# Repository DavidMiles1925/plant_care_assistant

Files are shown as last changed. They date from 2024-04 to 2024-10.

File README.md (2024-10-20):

# Plant Care Assistant

## Video

[Project Video Link](https://www.youtube.com/watch?v=mg84hZeF66U&t=700s)
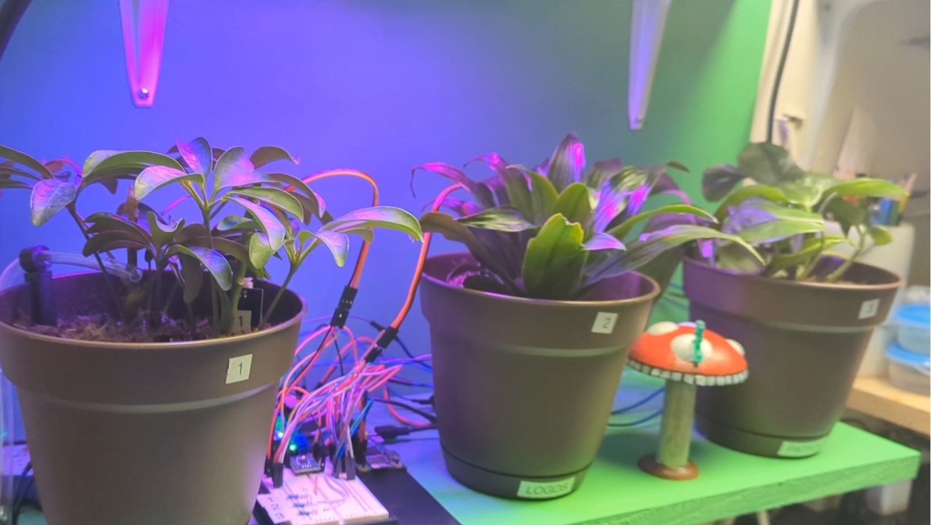
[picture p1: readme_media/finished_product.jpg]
Video Image


## Project Description

This project was developed to liven up my workspace. I wanted to have some plants, but historically I haven't kept them alive very well. I either over-water or under-water them. On top of that, my workspace gets no natural sunlight, so I wanted to make sure my plants got plenty of light. And lastly, my garage gets chilly in the winter, so I wanted my plants stay warm.

## Accepatance Criteria

**This project, when it is complete will:**

- ✔ Support up to 3 plants
- ✔ Monitor the moisture levels of the soil of each plant
- ✔ Water each plant when the soil is dry AND the soil has had an adequete period of dryness
- ✔ Provide adequete lighting for the plants with a timer function
- ✔ Log all metrics for debugging and historical reference
- **✔ NEW:** The amount of water dispensed can be counted from the logs programmatically

**Future State:**

- Provide gentle heat when soil temperature falls too low (future state)
- Smart lighting through feedback from a photo-resistor

## Seting up the Device

### Parts List

| Item | Quantity | Link |
| :--- | :---: | :--- |
| Raspberry Pi Zero 2 W (Any Pi will work) | 1 | [Microcenter](https://www.microcenter.com/product/643085/raspberry-pi-zero-2-w) |
| MicroSD card (For Raspberry Pi) | 1 | [Microcenter](https://www.microcenter.com/product/658767/micro-center-64gb-ultra-microsdxc-class-10-flash-memory-card-with-adapter) |
| 20x2 Pin Header for Raspberry Pi | 1 | [Microcenter](https://www.amazon.com/gp/product/B083DYVWDN/ref=ppx_yo_dt_b_search_asin_title?ie=UTF8&psc=1) |
| ADS7830 Analog-to-Digital Converter | 1 | No Link Available |
| Capacitive Moisture Sensor(s) |  1-3\* | [Amazon](https://www.amazon.com/gp/product/B07SYBSHGX/ref=ppx_yo_dt_b_search_asin_title?ie=UTF8&psc=1) |
| Water Pump(s) and Line |  1-3\* | [Amazon](https://www.amazon.com/gp/product/B07TMW5CDM/ref=ppx_yo_dt_b_search_asin_title?ie=UTF8&psc=1) |
| 5V USB Grow Light | 1 | [Amazon](https://www.amazon.com/gp/product/B0BXKWMTPF/ref=ppx_yo_dt_b_search_asin_title?ie=UTF8&psc=1) |
| 5V Relay |  2-4\* | [Amazon](https://www.amazon.com/gp/product/B09SLS3QT1/ref=ppx_yo_dt_b_search_asin_title?ie=UTF8&psc=1) |
| LED |  1-3\* | [Amazon](https://www.amazon.com/gp/product/B07QXR5MZB/ref=ppx_yo_dt_b_search_asin_title?ie=UTF8&psc=1) |
| 220 Ohm Reistor |  1-3\* | [Amazon](https://www.amazon.com/gp/product/B07ZX2CB6B/ref=ppx_yo_dt_b_search_asin_title?ie=UTF8&psc=1) |
| Solderless Breadboard | 1 | [Amazon](https://www.amazon.com/gp/product/B07PBFPJC6/ref=ppx_yo_dt_b_search_asin_title?ie=UTF8&psc=1) |
| Dupont Cables 10cm and 30cm | Many | [Amazon](https://www.amazon.com/gp/product/B01EV70C78/ref=ppx_yo_dt_b_search_asin_title?ie=UTF8&psc=1) |

\*Quantity is dependent on how many plants you want to care for.

### Diagram

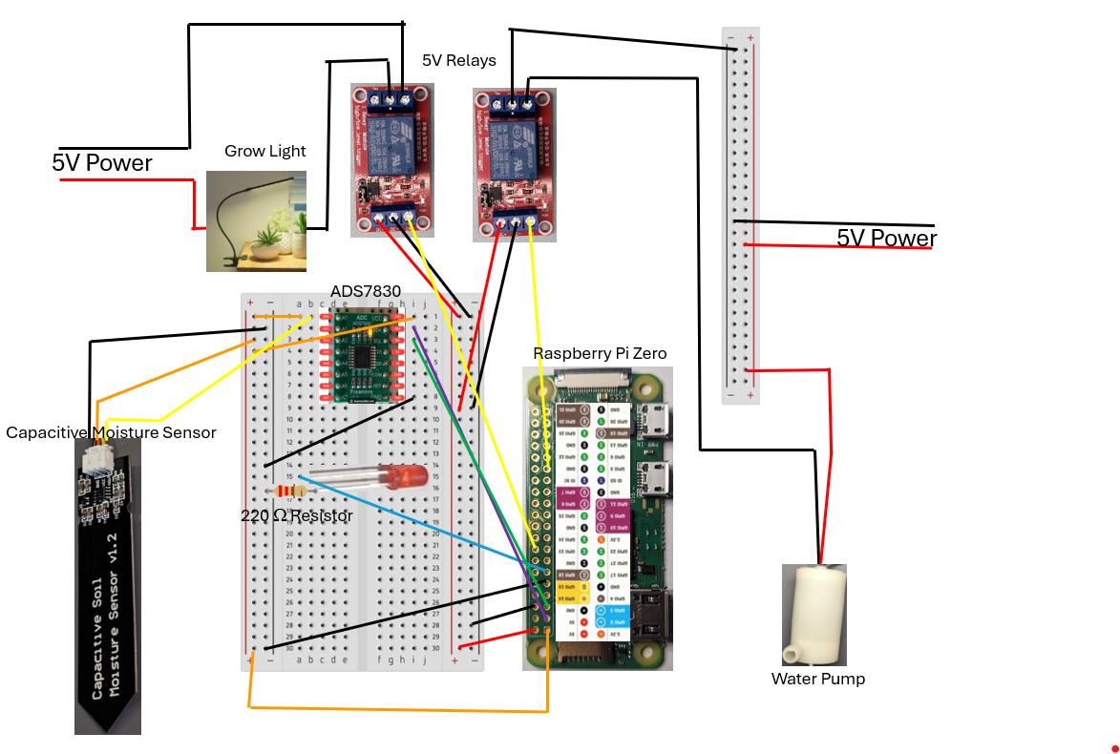
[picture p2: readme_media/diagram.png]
diagram


### Pin Assignments

**Note that all pins are in BCM mode**

| Component | Pi/Connection | Power |
| :--- | :---: | :---: |
| ADS7830 (or 1115) | 2, 3 |  3.3V (Pi) |
| Capacitive Moisture Sensor v 1.2 #1 | A0 (ADS) |  3.3V (Pi) |
| Capacitive Moisture Sensor v 1.2 #1 | A1 (ADS) |  3.3V (Pi) |
| Capacitive Moisture Sensor v 1.2 #1 | A2 (ADS) |  3.3V (Pi) |
| LED #1 | 17 |  3.3V (Pi) |
| LED #2 | 27 |  3.3V (Pi) |
| LED #3 | 22 |  3.3V (Pi) |
| Pump **Relay** #1 | 5 | 5V (Pi) |
| Pump **Relay** #2 (Optional) | 6 | 5V (Pi) |
| Pump **Relay** #3 (Optional) | 13 | 5V (Pi) |
| Light Relay #4 | 23 | 5V (Pi) |
| Water Pump #1 | Relay 1 | 5V (**USB**) |
| Water Pump #2 (Optional) | Relay 2 | 5V (**USB**) |
| Water Pump #3 (Optional) | Relay 3 | 5V (**USB**) |
| Light | Relay 4 | 5V (**USB**) |

### Set Up the Pi

[See my github tutorial on how to set up the Raspberry Pi Zero 2 W](https://github.com/DavidMiles1925/pi_zero_setup)

- If you want to run the code via SSH, make sure to also follow the instructions on that page on how to:
  [Set up a static IP address](https://github.com/DavidMiles1925/pi_zero_setup?tab=readme-ov-file#configure-static-ip-address)

### Set Up the Capacitive Moisture Sensor v1.2

1. Get the pins connected:  
   &emsp;See the [diagram](#diagram), [pin assignments](#pin-assignments), and [parts list](#parts-list) above.

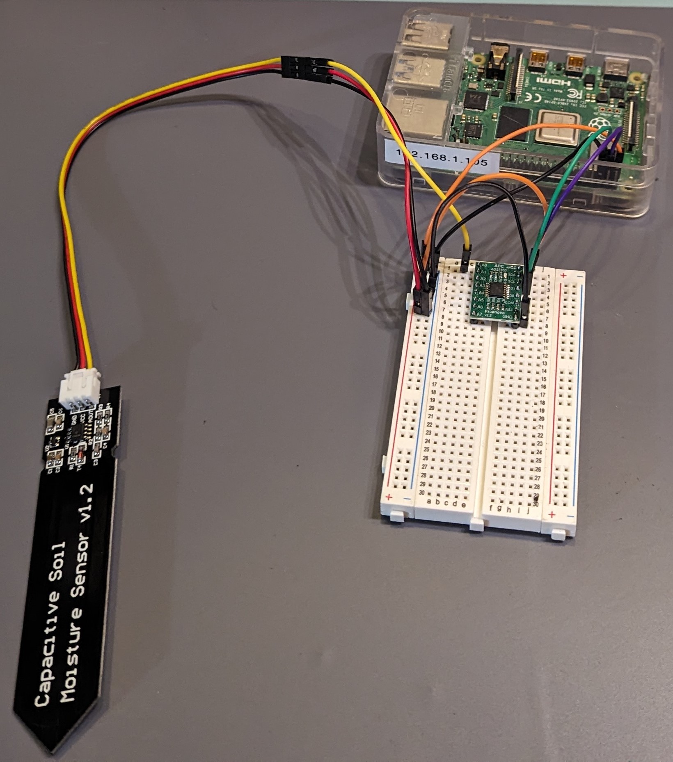
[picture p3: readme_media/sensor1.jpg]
sensor1

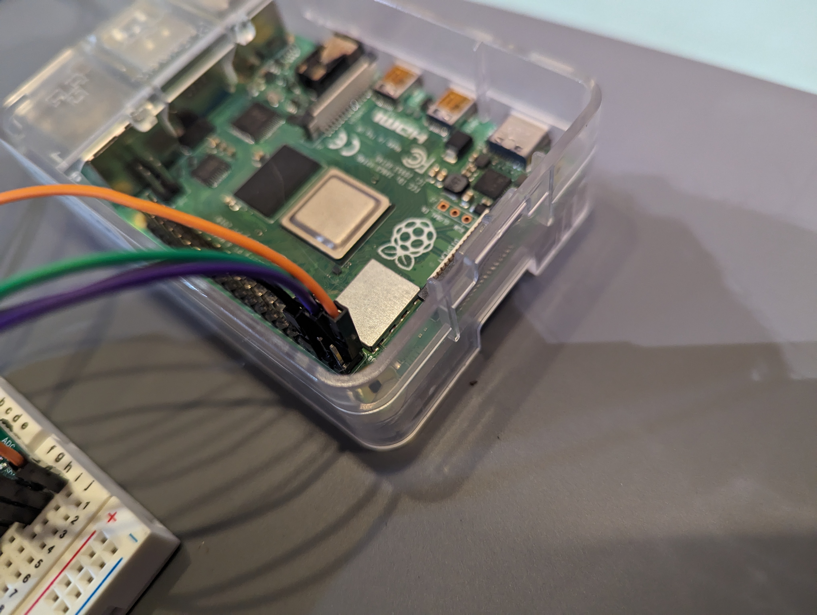
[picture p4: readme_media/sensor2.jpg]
sensor2


2. Make sure to calibrate your values with dry air, water, and everything in between (later after you get the code running):

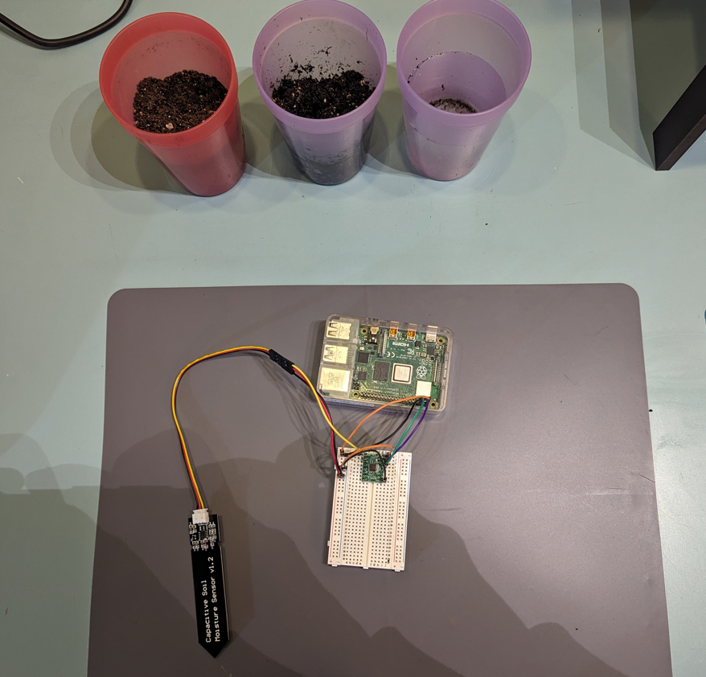
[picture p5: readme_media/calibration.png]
calibration


### Set Up Relays For Pumps

You'll need to wire up the relays as shown in the [diagram](#diagram).

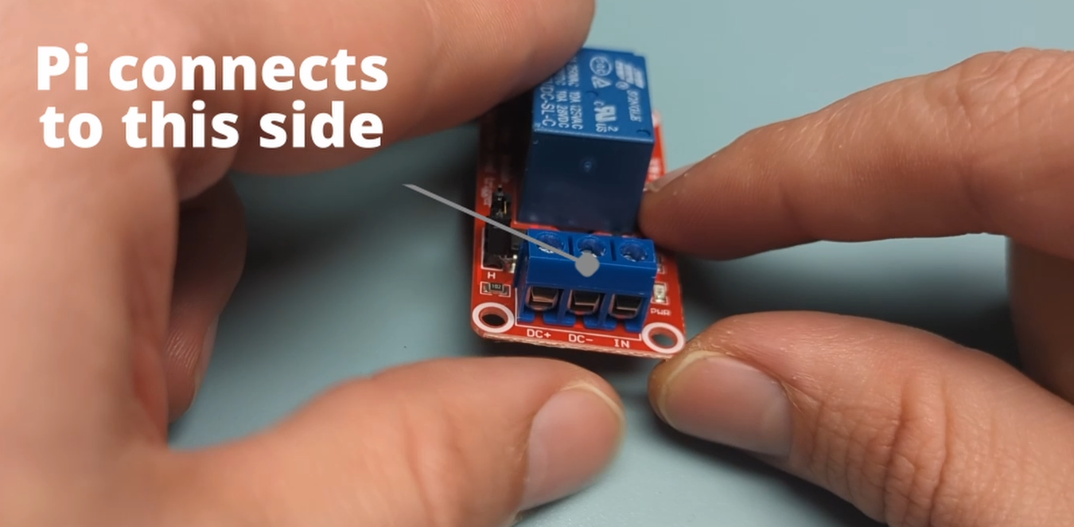
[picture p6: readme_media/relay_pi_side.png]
relay_pi_side


- `DC+` may be labeled as `VCC`
- `DC-` may be labeled as `GND`
- `IN` may be labeled as `PIN`

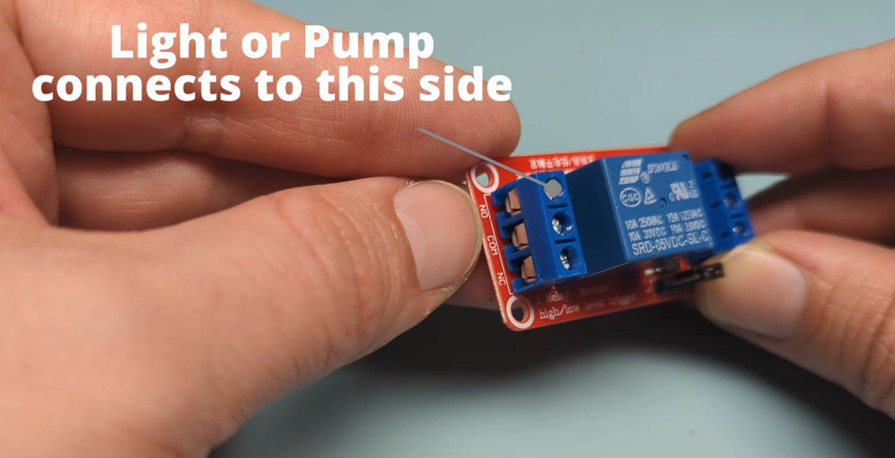
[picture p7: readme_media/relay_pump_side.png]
relay_pump_side


- Use the `NO` and `COM` ports. The NC port will turn the circuit on by default.

### Set Up the Pumps

1. Wire up the power for the pump using batteries or a USB cable. **DO NOT POWER THESE PUMPS DIRECTLY WITH THE PI!!!**

**See the [Video](#video) for tips on working with the tiny leads on the pump.**

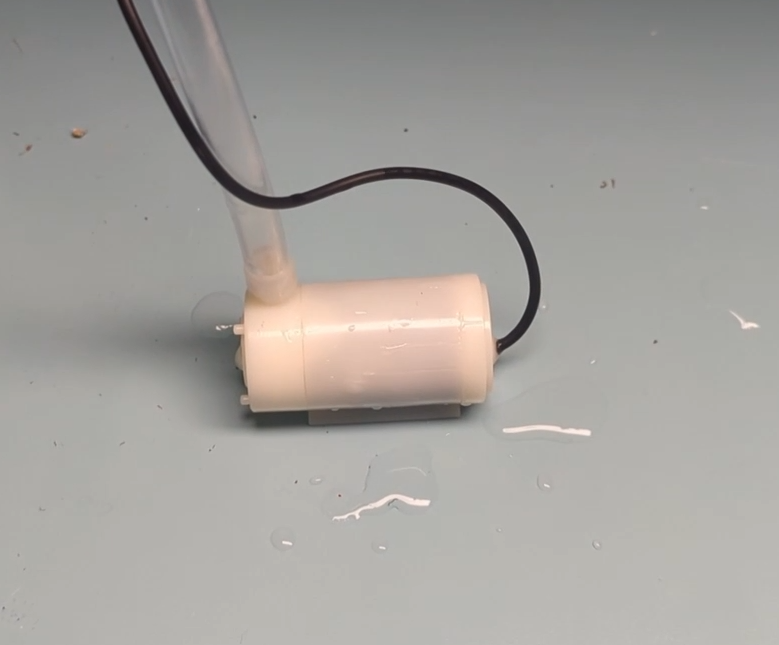
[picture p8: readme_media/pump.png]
pump

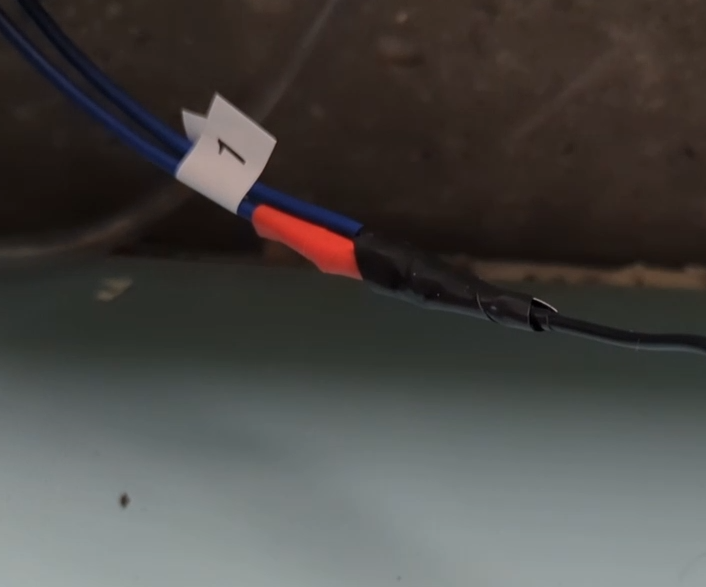
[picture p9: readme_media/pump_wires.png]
pump_wires

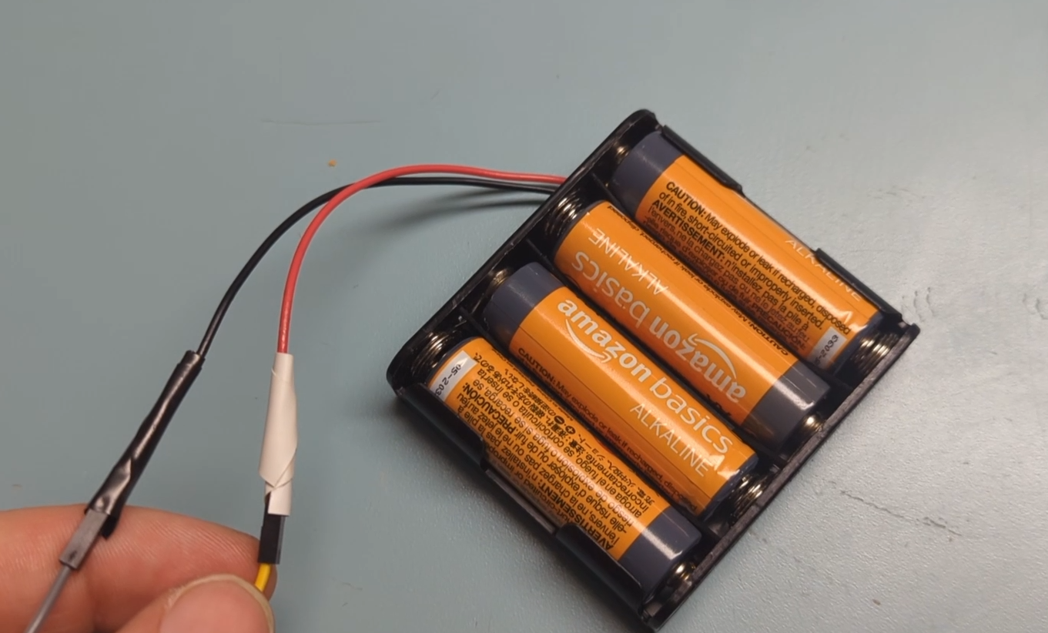
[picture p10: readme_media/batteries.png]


2. Connect pumps to relays. See [pins](#pin-assignments) above for hookup to Pi.

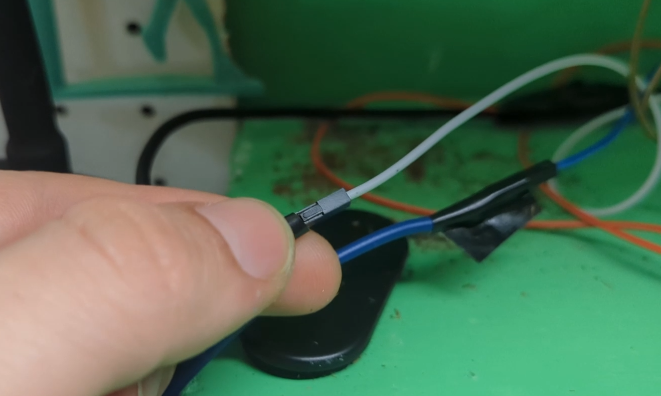
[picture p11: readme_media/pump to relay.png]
pump_to_relay


3. **Ensure your wires are guarded from any contact with the water.**

4. (Optional) Print the Water Tank from the [3D_prints_files](https://github.com/DavidMiles1925/plant_care_assistant/tree/main/3D_print_files) folder at the top of the page.

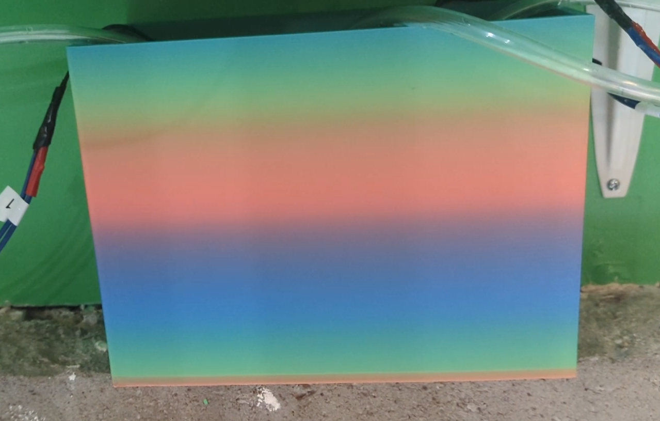
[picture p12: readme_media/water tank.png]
water_tank


5. (Optional) Print the Plant Pot Hose Clips from the [3D_prints_files](https://github.com/DavidMiles1925/plant_care_assistant/tree/main/3D_print_files) folder at the top of the page.

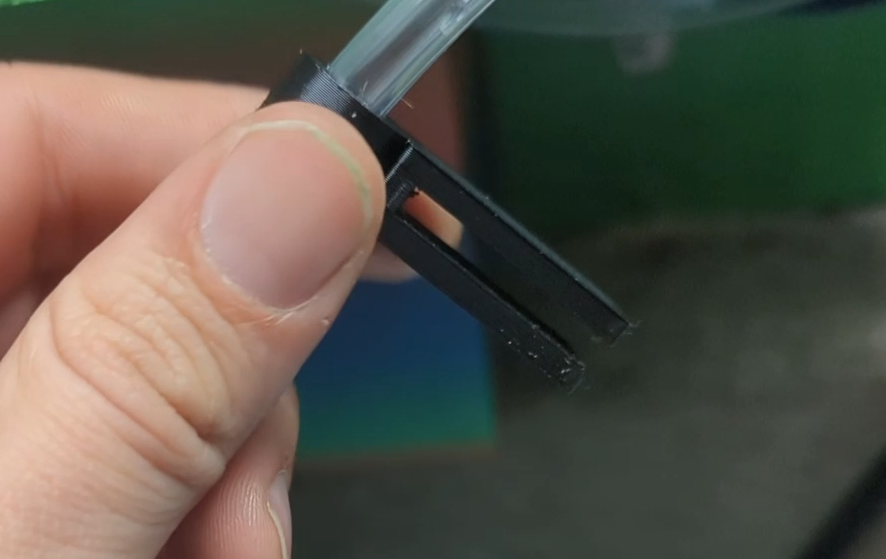
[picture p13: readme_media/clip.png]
hose_clip


6. Hook your hose up to the pumps, and run them to the pot.

### Set Up the Light

1. The light is powered just like the [pumps](#set-up-the-pumps), in that it needs to be powered by an external power source. **NOT THE PI!**

2. The light connects to a [relay](#set-up-relays-for-pumps) the same way the pumps do.

3. **See the [video](#video) for information about removing the module on the light.**

### Set Up I2C/smbus

1. From the Raspberry Pi terminal, run the following command:

```bash
sudo raspi-config
```

- Select Option 3: Interface Options
- Enable `ARM I2C`

2. Install `smbus`

```bash
sudo apt-get install python3-smbus
```

### Install Git and Code

1. From the Raspberry Pi terminal, run the following command:

```bash
sudo apt-get install git
```

- Make sure to push an uppercase `Y` when you select "yes" to installing.

2. Clone the code to your Pi by entering the following command.

```bash
git clone https://github.com/DavidMiles1925/plant_care_assistant.git
```

### Navigate to the Directory

- After installing your code:

```bash
cd plant_care_assistant
```

### Configuring the Program

Configuration instructions coming soon.

See the video for a detailed walkthrough of the configuration values.

### Run the Program

- Run the program

```bash
sudo python plant.py
```

### Accessing the Logs

- Navigate to `/logs` directory

```bash
cd logs/
```

- Check log names

```bash
ls
```

- Open logs

```bash
sudo nano FILENAME.txt
```

- Basic nano navigation

More detailed info coming soon. Check out the [video](#video) for more details.

### Counting the Log Files

I've added a script called `log_counter.py`.

The purpose of this script is to count the number of times water was dispensed from each sensor, based on the logs in the `logs/` directory.

## Gallery

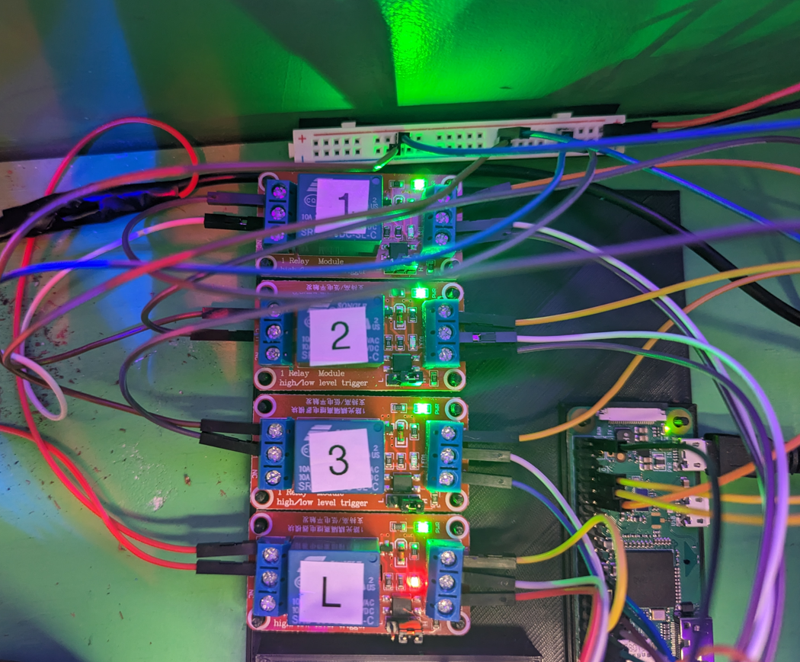
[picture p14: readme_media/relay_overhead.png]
Overhed


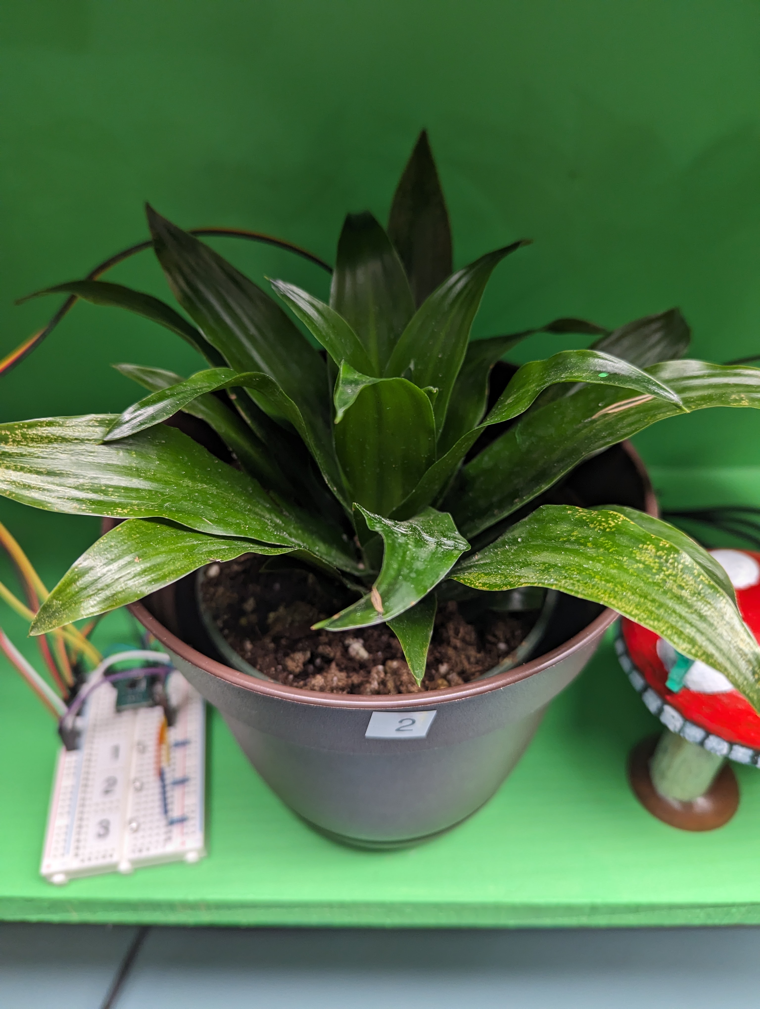
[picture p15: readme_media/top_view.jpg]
Top View


## Acknowldegements

### Picture of ADS7830

Picture source: (https://www.js4iot.com/2021/06/06/ADC_RPIO.html)

This picture is such a wonderful representation of the ADS7830. Check out the link above, this developer uses JavaScript for his code, something I've never even done with a Pi! So cool.

### Background Music for Intro

Music I use: https://www.bensound.com  
License code: WUITXNB2OK8EGMAO

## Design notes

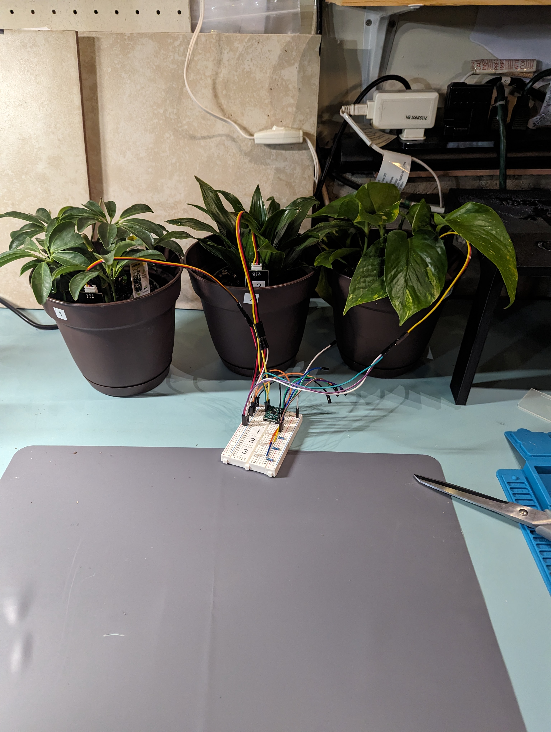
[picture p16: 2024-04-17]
readme_media/first_time_remote.jpg

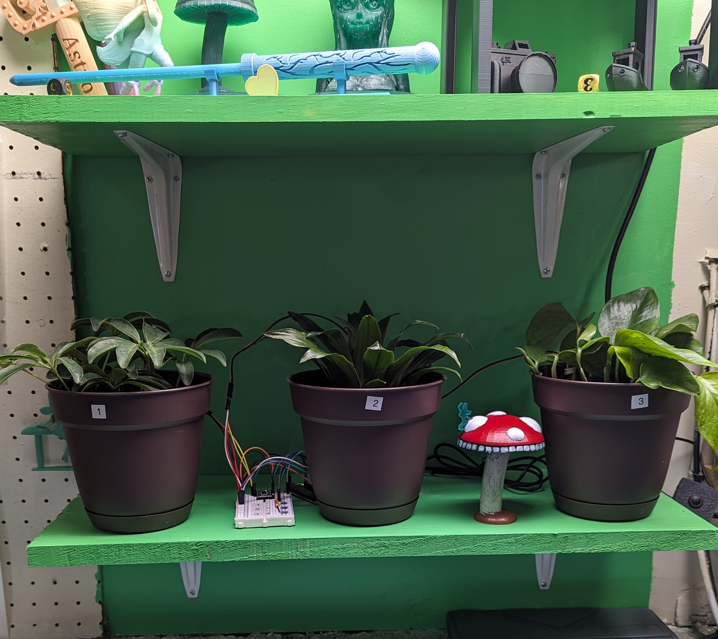
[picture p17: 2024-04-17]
readme_media/on_the_shelf.jpg

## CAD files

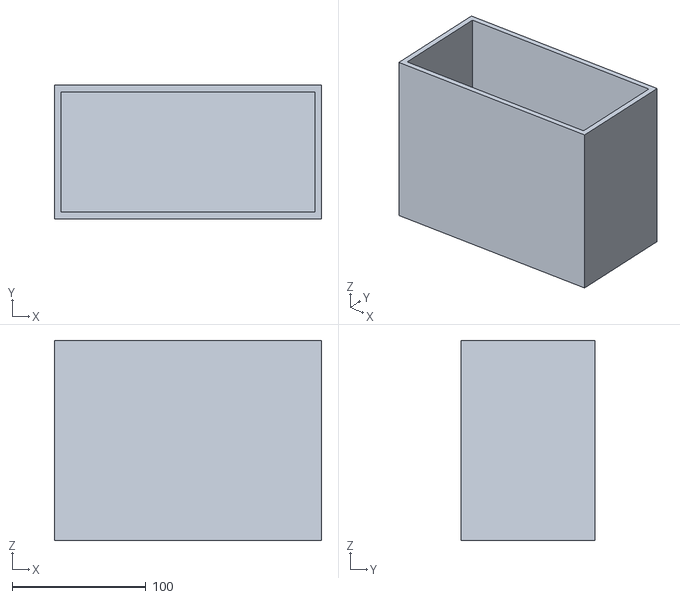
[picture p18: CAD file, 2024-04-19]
3D_print_files/Water Tank.stl
200.0 x 100.0 x 150.0

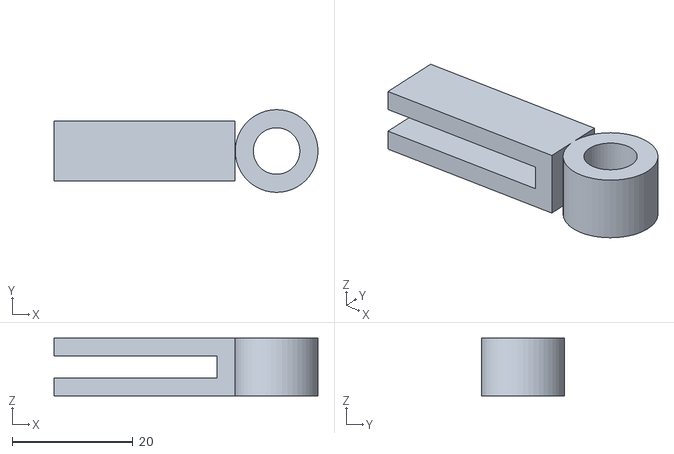
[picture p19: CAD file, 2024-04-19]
3D_print_files/Plant Pot Hose Clip.stl
43.7 x 13.7 x 9.60

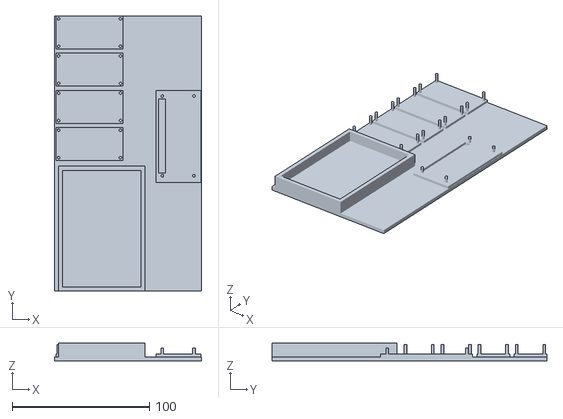
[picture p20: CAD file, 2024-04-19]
3D_print_files/Pi Plant Computer Beta.stl
107.0 x 200.0 x 13.0

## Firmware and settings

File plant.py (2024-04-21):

import os
import RPi.GPIO as GPIO
import subprocess
from smbus import SMBus
from datetime import datetime
from time import sleep

from config import ADS_BYTE_ADDRESS,\
            ADS_COMMANDS, \
            CLEAR_SCREEN_BEFORE_PRINT, \
            DRY_COUNT_BEFORE_WATERING, \
            DURATION_BETWEEN_CHECKS, \
            DRY_SOIL_VALUE, \
            DRY_VALUE, \
            LED_ARRAY_WATER_STATUS, \
            LIGHT_SCRIPT_PATH, \
            MOIST_SOIL_VALUE, \
            NUMBER_OF_ANALOG_INPUTS, \
            OPENING_MESSAGE, \
            PUMP_ON_TIME, \
            WET_SOIL_VALUE, \
            WATER_VALUE, \
            WATER_IF_DRY, \
            WATER_PUMP_ARRAY
            
from logger import console_and_log

# Bus
bus = SMBus(1)

# List that will be used to keep track of 
is_dry_list = []

def check_if_water_is_needed(analog_input):
    global is_dry_list

    if is_dry_list[analog_input] >= DRY_COUNT_BEFORE_WATERING and WATER_IF_DRY:
        water_plant(analog_input)





def determine_soil_moisture(value, analog_input):
    global is_dry_list

    if value >= DRY_VALUE:
        is_dry_list[analog_input] = is_dry_list[analog_input] + 1
        GPIO.output(LED_ARRAY_WATER_STATUS[analog_input], GPIO.HIGH)
        return "Dry: No Soil"
    
    elif value >= DRY_SOIL_VALUE:
        is_dry_list[analog_input] = is_dry_list[analog_input] + 1
        GPIO.output(LED_ARRAY_WATER_STATUS[analog_input], GPIO.HIGH)
        return "Dry Soil    "
    
    elif value >= MOIST_SOIL_VALUE:
        is_dry_list[analog_input] = 0
        GPIO.output(LED_ARRAY_WATER_STATUS[analog_input], GPIO.LOW)
        return "Moist Soil  "
    
    elif value >= WET_SOIL_VALUE:
        is_dry_list[analog_input] = 0
        GPIO.output(LED_ARRAY_WATER_STATUS[analog_input], GPIO.LOW)
        return "Wet Soil    "
    
    elif value >= WATER_VALUE:
        is_dry_list[analog_input] = 0
        GPIO.output(LED_ARRAY_WATER_STATUS[analog_input], GPIO.LOW)
        return "Water       "
    else:
        return "Low Value"


def output_sensor_data(value, status, analog_input):
    global is_dry_list

    console_and_log(f"Sensor: {analog_input+1}\t{status}\t\t({value})\t\t[count: {is_dry_list[analog_input]}]")
    #console_and_log(f"{status}")


def read_sensor(input):
    bus.write_byte(ADS_BYTE_ADDRESS, ADS_COMMANDS[input])
    return bus.read_byte(ADS_BYTE_ADDRESS)


def setup_pins():
    # Board Mode: BCM
        GPIO.setmode(GPIO.BCM)

        # Disable Warnings
        GPIO.setwarnings(False)

        for led in range(len(LED_ARRAY_WATER_STATUS)):
            GPIO.setup(LED_ARRAY_WATER_STATUS[led], GPIO.OUT)
            GPIO.output(LED_ARRAY_WATER_STATUS[led], GPIO.HIGH)

        for pin in range(len(WATER_PUMP_ARRAY)):
            GPIO.setup(WATER_PUMP_ARRAY[pin], GPIO.OUT)
            GPIO.output(WATER_PUMP_ARRAY[pin], GPIO.LOW)


def toggle_pump(value, analog_input):
    GPIO.output(WATER_PUMP_ARRAY[analog_input], value)


def water_plant(analog_input):
    global is_dry_list

    toggle_pump(True, analog_input)

    sleep(PUMP_ON_TIME)

    toggle_pump(False, analog_input)

    console_and_log(f"*****WATER DISPENSED: Sensor {analog_input + 1}*****")

    is_dry_list[analog_input] = 0


if __name__ == "__main__":
    try:
        # Start script to turn the light on/off at specified time.
        subprocess.Popen(["sudo", "python", LIGHT_SCRIPT_PATH])

        setup_pins()

        os.system("clear")

        console_and_log(OPENING_MESSAGE)
        
        # Set up a counter for each moisture sensor to keep track of how long they have been dry.
        for input_counter in range(NUMBER_OF_ANALOG_INPUTS):
            is_dry_list.append(1)

        while True:

            # Collect metrics for each input and water plants if necessary
            for analog_input in range(NUMBER_OF_ANALOG_INPUTS):
                sensor_value = read_sensor(analog_input)

                soil_status = determine_soil_moisture(sensor_value, analog_input)
                
                output_sensor_data(sensor_value, soil_status, analog_input)

                check_if_water_is_needed(analog_input)


            sleep(DURATION_BETWEEN_CHECKS)

            if CLEAR_SCREEN_BEFORE_PRINT:
                os.system("clear")

    except Exception as e:
        console_and_log(f"An exception was caught in the main function: {e}\n\n\n")
        GPIO.cleanup()

    except KeyboardInterrupt:
        console_and_log(f"The moisture program was terminated using Ctrl+C\n\n\n")
        GPIO.cleanup()

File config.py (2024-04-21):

##########        Main Control Variables          ##########

PI_USERNAME = "bulbasaur"       # This is the username you log into your pi with.
NUMBER_OF_ANALOG_INPUTS = 3     # Maximum 3
DURATION_BETWEEN_CHECKS = 1800    # Time in seconds
DRY_COUNT_BEFORE_WATERING = 6   # How many times should a "dry" result be returned before the plant is watered?
WATER_IF_DRY = True             # Should the plant(s) be watered if it is dry?


##########               Lighting                 ##########

LIGHT_RELAY_PIN = 23
LIGHT_START_TIME_ARRAY = ["08:00:00", "10:00:00", "12:00:00", "14:00:00", "16:00:00", "18:00:00"]      # Format must be HH:MM:SS, 24 hr format
LIGHT_DURATION = 900              # Time in seconds
LIGHT_SCRIPT_PATH = f"/home/{PI_USERNAME}/plant_care_assistant/light.py"
LED_ARRAY_WATER_STATUS = [17, 27, 22]


##########      Capacitive Moisture Sensor        ##########

DRY_VALUE = 215
DRY_SOIL_VALUE = 195
MOIST_SOIL_VALUE = 160
WET_SOIL_VALUE = 115
WATER_VALUE = 100


##########               Water Pump              ##########

PUMP_ON_TIME = 1                # Time in seconds
WATER_PUMP_ARRAY = [5, 6, 13]


##########   ADS7830 (Or ADS1115) Analog-to-Digtal Converter   ##########


# Input Number:  0     1     2     3     4     5     6     7
#---------------------------------------------------------------
ADS_COMMANDS = [0x84, 0xc4, 0x94, 0xd4, 0xa4, 0xe4, 0xb4, 0xf4]
ADS_BYTE_ADDRESS = 0x4b

# To use the ADS1115, comment out the above constants, and uncomment the constants below.

#ADS_COMMANDS = [0x49, 0x4A, 0x4B, 0x4C]
#ADS_BYTE_ADDRESS = 0x48


##########             Welcome Message            ##########

OPENING_MESSAGE = f"\n******************************************************************\n\nMain Program Started\n\nPlant will be watered when dry: {WATER_IF_DRY}\nCheck will be made every {DURATION_BETWEEN_CHECKS} seconds.\n\nCalibration Values:\nDry:\t\t{DRY_VALUE}\nDry Soil:\t{DRY_SOIL_VALUE}\nMoist Soil:\t{MOIST_SOIL_VALUE}\nWet Soil:\t{WET_SOIL_VALUE}\nWater:\t\t{WATER_VALUE}\n\n********************************************"
LIGHT_LOG_MESSAGE = f"\n\nLight Control Subprocess Started\n\nLight relay is using pin {LIGHT_RELAY_PIN}\nLight will turn on at {LIGHT_START_TIME_ARRAY}\nIt will remain on for {LIGHT_DURATION} seconds\n\n********************************************"

##########      Console Output and Logging        ##########

LOG_DIRECTORY_PATH = f"/home/{PI_USERNAME}/plant_care_assistant/logs"

CONSOLE_OUTPUT_ON = True
LOGGING_ENABLED = True

CLEAR_SCREEN_BEFORE_PRINT = True

##########                Reference               ##########

# Seconds in a
#       Hour:   3600
#       Day:    86,400
#       Week:   604,800

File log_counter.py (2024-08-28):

import os
from config import LOG_DIRECTORY_PATH

def count_water_dispensed(directory):
    # Initialize counters
    one_counter = 0
    two_counter = 0
    three_counter = 0

    # Iterate over each file in the specified directory
    for filename in os.listdir(directory):
        if os.path.isfile(os.path.join(directory, filename)):
            with open(os.path.join(directory, filename), 'r') as file:
                # Read the file line by line
                for line in file:
                    # Look for the text "WATER DISPENSED:"
                    if "WATER DISPENSED:" in line:
                        # Find the position of "WATER DISPENSED:"
                        index = line.find("WATER DISPENSED:")
                        # Get the character 9 spaces to the right of it
                        char = line[index + 24]  # 25 = len("WATER DISPENSED:") + 9
                        # Increment the appropriate counter
                        if char == '1':
                            one_counter += 1
                        elif char == '2':
                            two_counter += 1
                        elif char == '3':
                            three_counter += 1

    # Print the results
    print(f"Count of '1': {one_counter}")
    print(f"Count of '2': {two_counter}")
    print(f"Count of '3': {three_counter}")


if __name__ == "__main__":

    # Set directory path appropriately
    directory_path = LOG_DIRECTORY_PATH

    # For windows...
    # directory_path = "C:/Users///"

    # Count the number of times water was dispensed for each sensor
    count_water_dispensed(directory_path)

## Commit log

2024-04-14 add multiple channels and LED indicators
2024-04-18 add water pump functionality
2024-04-19 add username and pump on time to config
2024-04-19 add 3d print files
    [Pi Plant Computer Beta.stl, Plant Pot Hose Clip.stl, Water Tank.stl]
2024-04-21 fix 1115 values and readme update
    [config.py, plant.py]
2024-04-21 readme update add pump instrusctions
2024-08-28 remove print()s from log_counter
2024-10-20 readme: correct calibration pic
